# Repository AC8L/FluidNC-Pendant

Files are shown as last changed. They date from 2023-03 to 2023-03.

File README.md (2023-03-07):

# FluidNC-Pendant
Work originated from https://github.com/gjkrediet/Fluid-controller

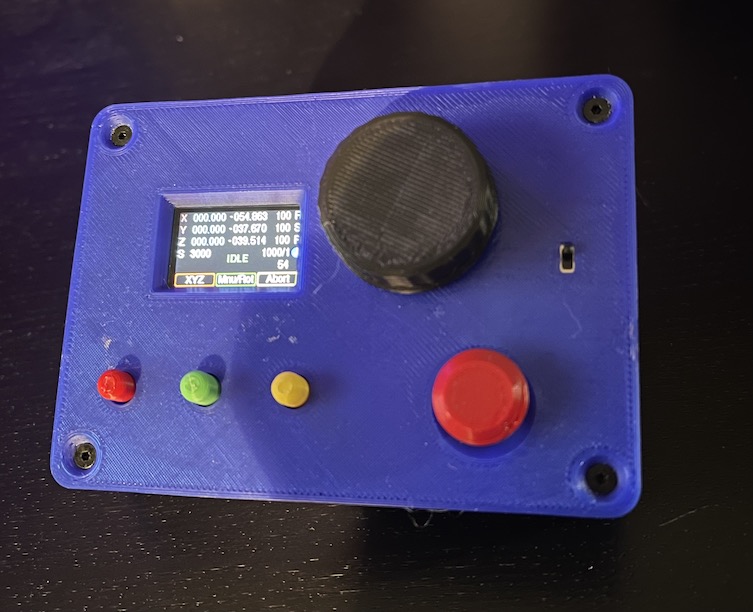
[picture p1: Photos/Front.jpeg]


The original design by gjkrediet was intended for bluetooth, this design is for Wi-Fi version of the FluidNC. Pendant communicates with the controller through Websocket protocol on TCP port 81.

# PCB
PCB was redesigned to hold all components to be soldered into it except the battery and power switch.
GRBL files are included for online order as well as schematics.

## Front of the PCB with soldered components
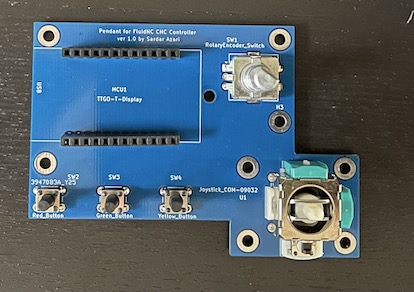
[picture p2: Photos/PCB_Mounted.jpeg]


## Back of the PCB
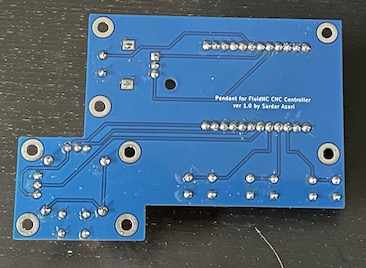
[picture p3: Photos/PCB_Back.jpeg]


## JST 2.0 soldered to the power switch and JST that comes with TTGO
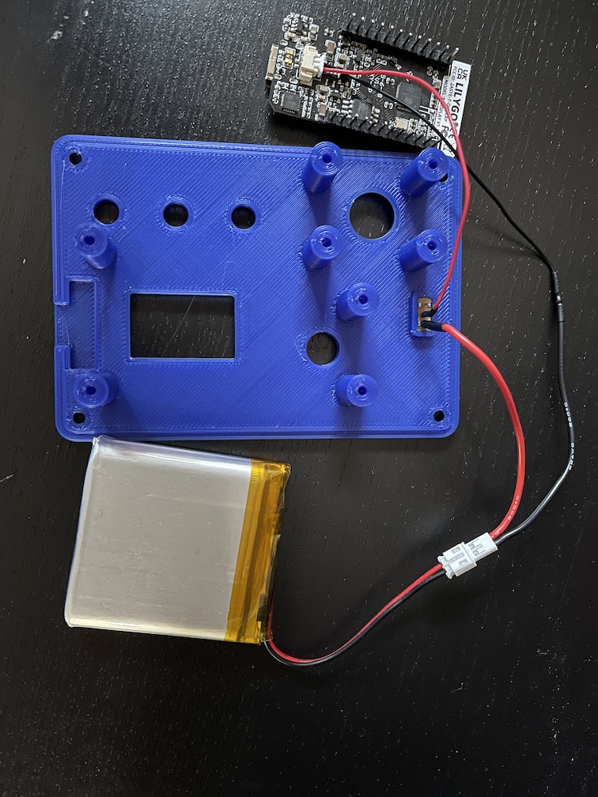
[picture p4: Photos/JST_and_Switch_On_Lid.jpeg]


## Battery is fixed behind PCB with a Kapton tape
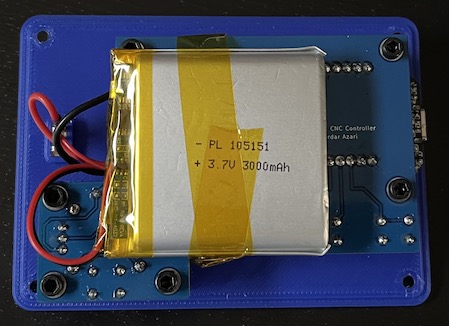
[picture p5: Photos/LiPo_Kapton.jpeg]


# 3D printed case
Lid was slightly modified to hold new PCB and power switch. Depending on which tactile switches were used - 3D printed buttons can be vertically scaled/reduced in the slicer.

# Firmware
Development was migrated from Arduino IDE into the PlatformIO to have stricter control over library versioning.
## Installation instructions:
1. Clone git repo: git clone https://github.com/AC8L/FluidNC-Pendant.git
2. Copy/rename sample_Config.h to Config.h
3. Enter your WiFi SSID information and FluidNC hostname/port in Config.h
4. Wait until Visual Studio Code pulls down all depending libraries
5. Overwrite content of .pio/libdeps/esp32dev/TFT_eSPI/User_Setup.h with the content of User_Setup.h.TFT_eSPI
6. Overwrite the content of .pio/libdeps/esp32dev/TFT_eSPI/User_Setup_Select.h with the content of User_Setup_select.h.TFT_eSPI
7. Now firmware will compile and you should be able to program the TTGO T Display.

# Operations
This section should probably be the largest section of this document but let at least get started.

## Red button
- When FluidNC is in ALARM mode, pressing RED button sends UNLOCK command
- Long pressing the RED button puts pendant into the sleep mode
- When in sleep mode, pressing RED button wakes pendant up

## Optical rotator
- By default it is in the mode of adjusting the jog speed
- When pressed - it enters the Menu mode. Menu options can be selected on the screen by scrolling the rotator and finally choosing by a click
- Homing can be done from Menu and changing brightness, turning spindle on and off among other functions

## Joystick
Jogs X and Y axes

## Green button
- Pressing GREEN button allows to change the default parameter that rotator controls.
- For example, after pressing the green button by rotating the rotator we can select the Z access to be controlled by rotator. Then we make a selection by pressing the GREEN button again and use rotator to bring the Z axis up and down.
## Yellow Button
Sends abort commands to the CNC

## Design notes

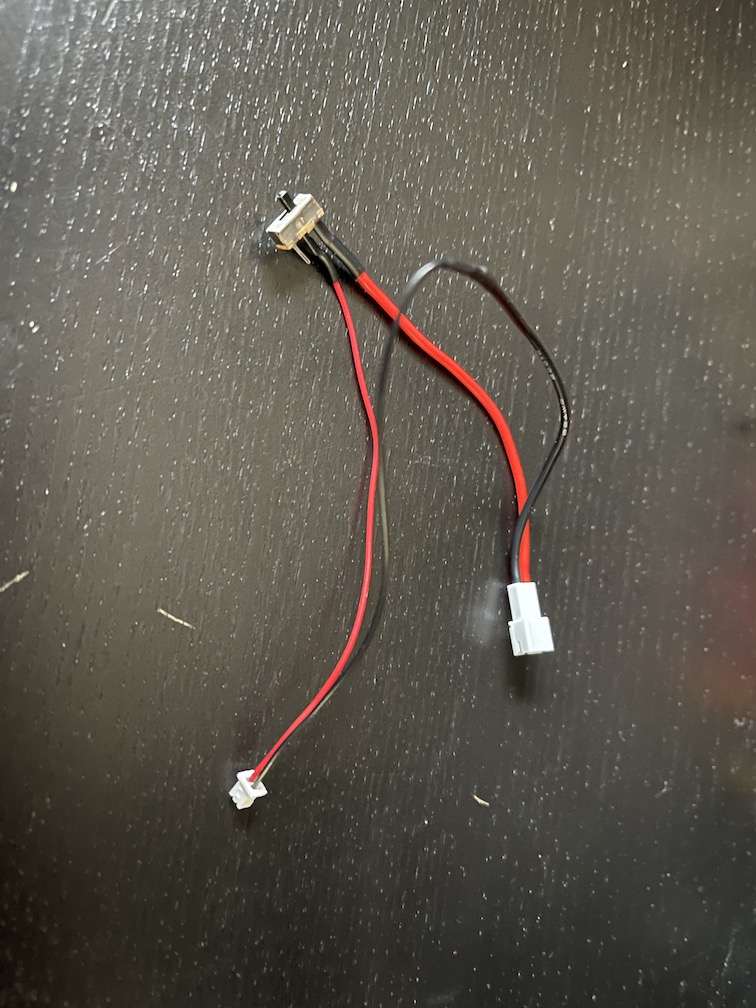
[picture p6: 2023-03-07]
Photos/JST_and_Switch.jpeg

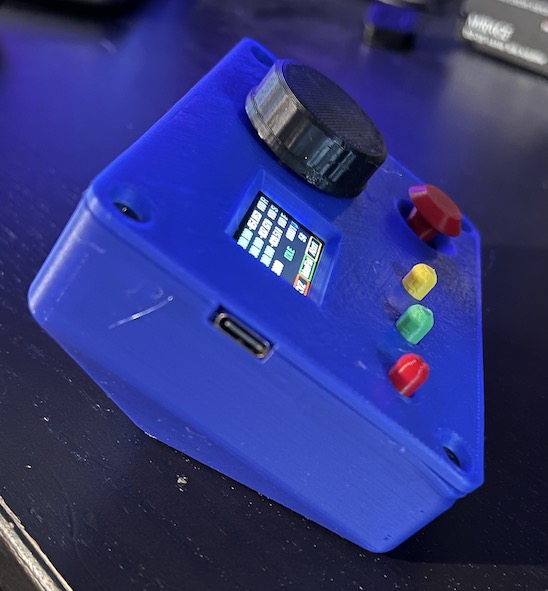
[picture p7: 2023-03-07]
Photos/Left.jpeg

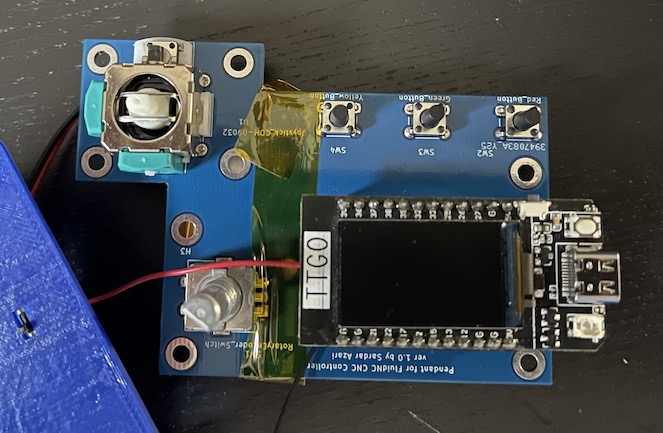
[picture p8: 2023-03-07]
Photos/Before fixing to lid.jpeg

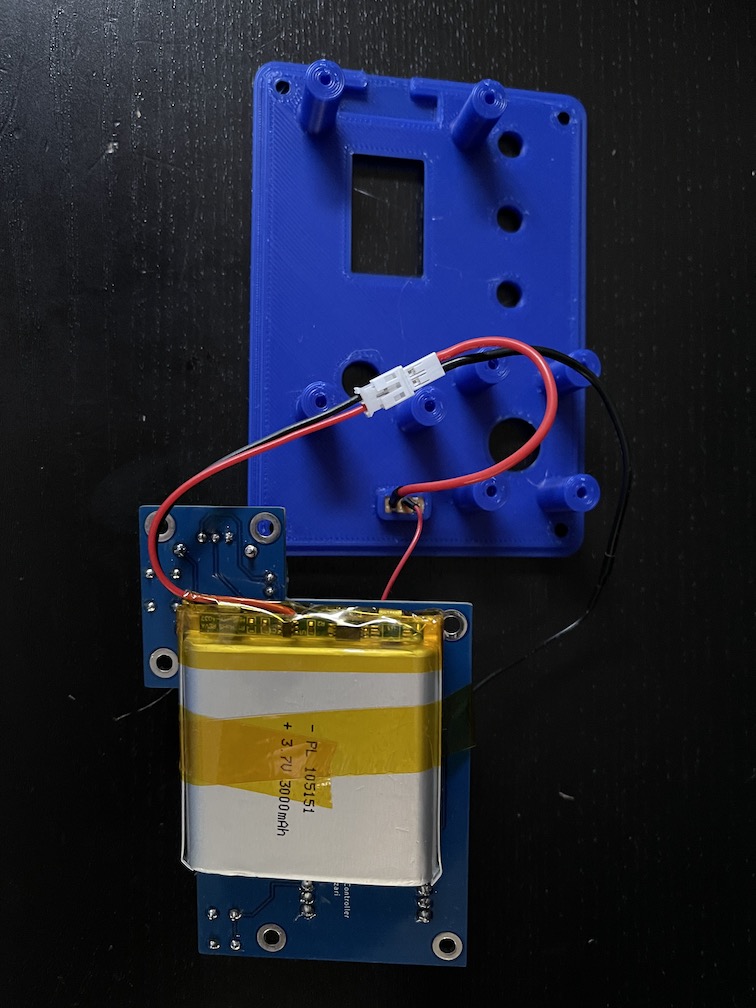
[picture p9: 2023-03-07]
Photos/BatteryAttached.jpeg

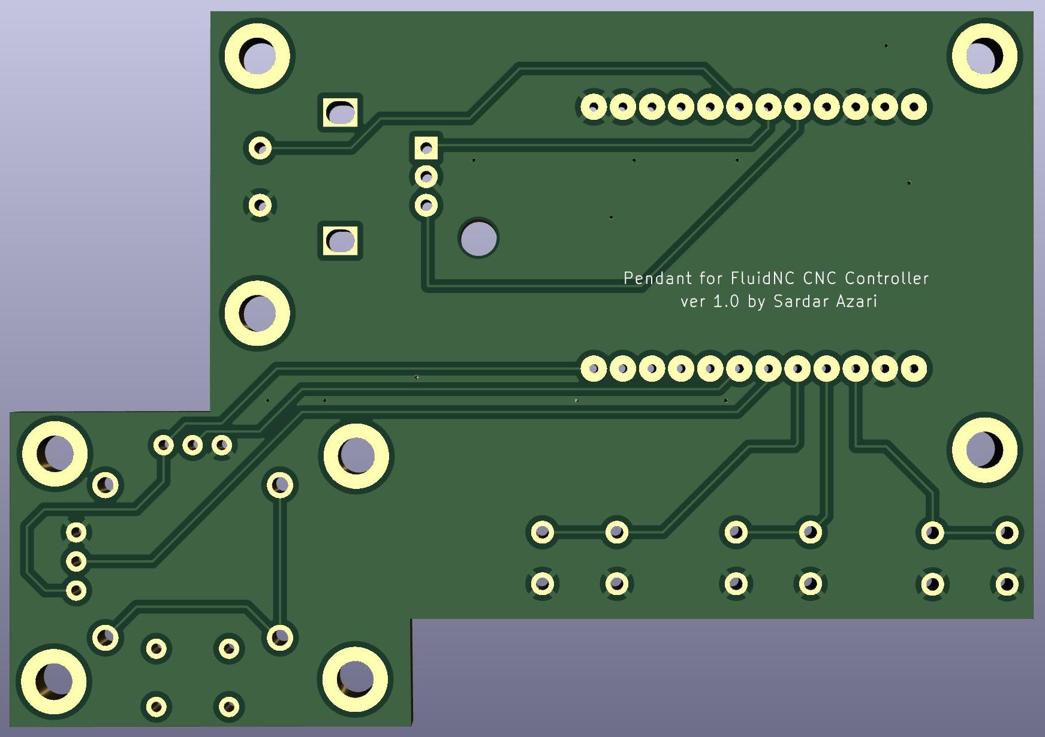
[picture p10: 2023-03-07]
PCB/FluidNC_Pendant_v2_Bottom.jpg

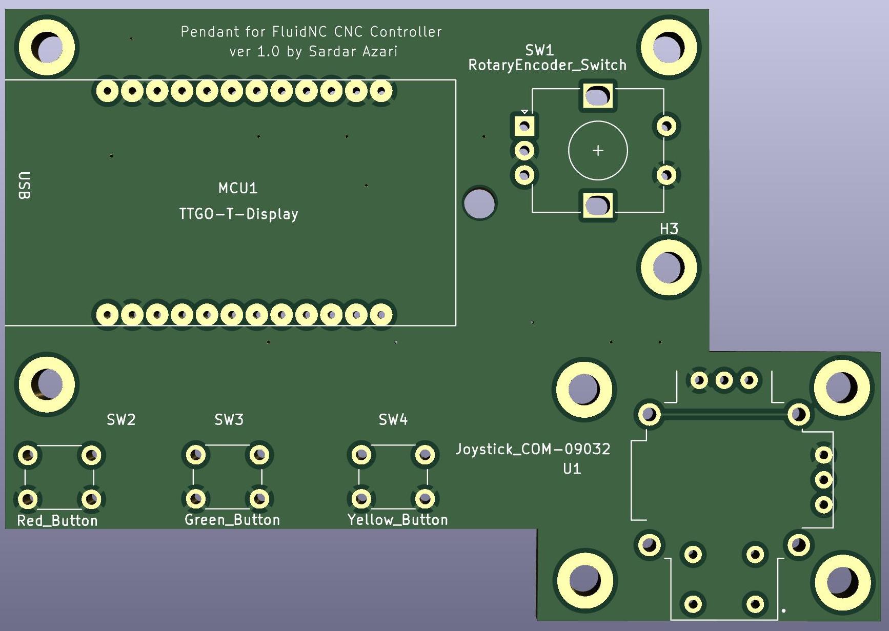
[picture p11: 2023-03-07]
PCB/FluidNC_Pendant_v2_Top.jpg

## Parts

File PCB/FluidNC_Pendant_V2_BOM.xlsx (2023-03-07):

Designator | Qnty | Description | Vendor/Link
MCU1 | 1 | LILYGO ESP32 T-Display Module | https://a.co/d/arEl3ou
SW1 | 1 | EC11 Rotary Encoder with switch | https://a.co/d/4C1LfQT
U1 | 1 | Joystick, 2 - Axis Analog (Resistive) Output | https://www.digikey.com/en/products/detail/sparkfun-electronics/COM-09032/6823623
SW2,SW3,SW4 | 3 | Tactile Switch SPST-NO Top Actuated Through Hole | https://www.digikey.com/en/products/detail/e-switch/TL1105DF160Q/271562
Battery | 1 | 3000mAh 105151 Lipo Battery with PH2.0mm JST Connector | https://a.co/d/7y6UerZ
JST | 1 | JST-PH 2.0 Female Connector Cable | https://a.co/d/fxLiYQF
SW5 | 1 | Switch, single pole double throw | https://www.digikey.com/en/products/detail/nkk-switches/MS12ANG03/1052824
 | 2 | 12 pin female head strip | https://a.co/d/bCoLMiA

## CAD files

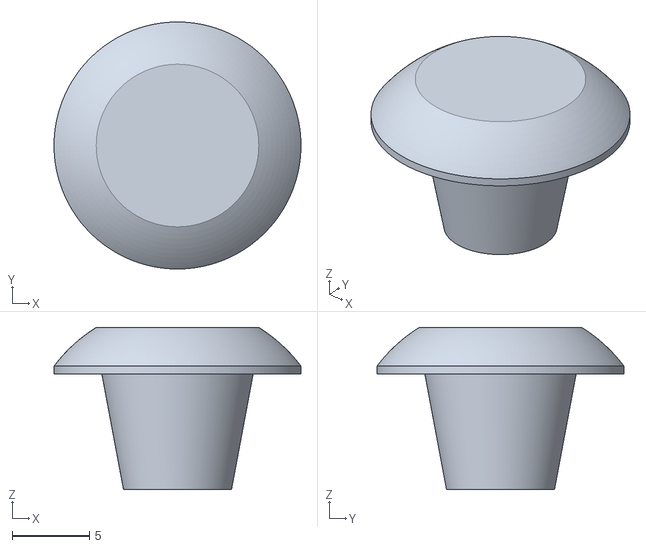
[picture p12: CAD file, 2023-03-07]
3D_Case/JoyStickKnob.stl
16.0 x 16.0 x 10.5

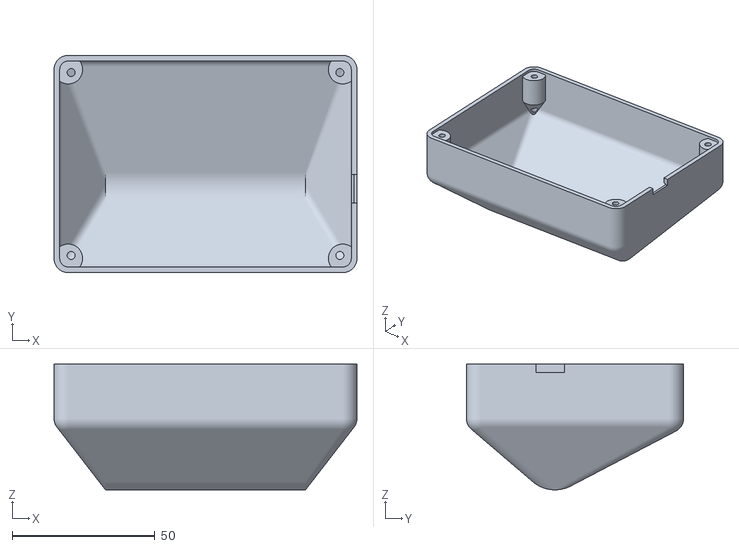
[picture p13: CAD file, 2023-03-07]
3D_Case/pendantV2_case.stl
106.0 x 76.0 x 44.0

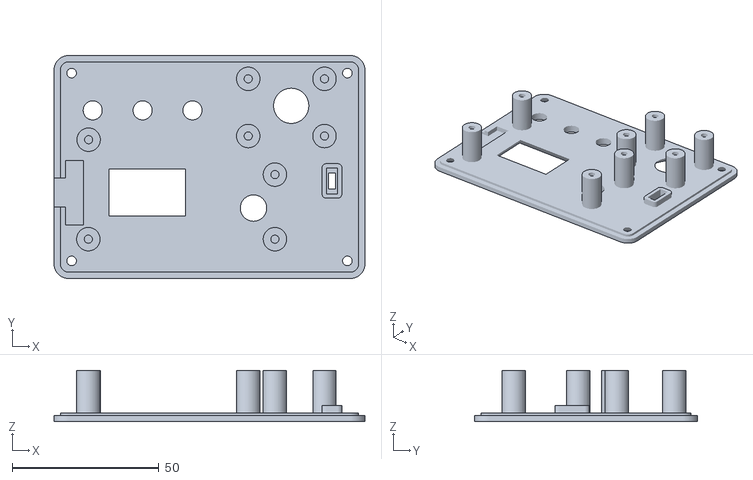
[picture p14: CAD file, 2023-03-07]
3D_Case/pendantV3_lid.stl
106.0 x 76.0 x 17.5

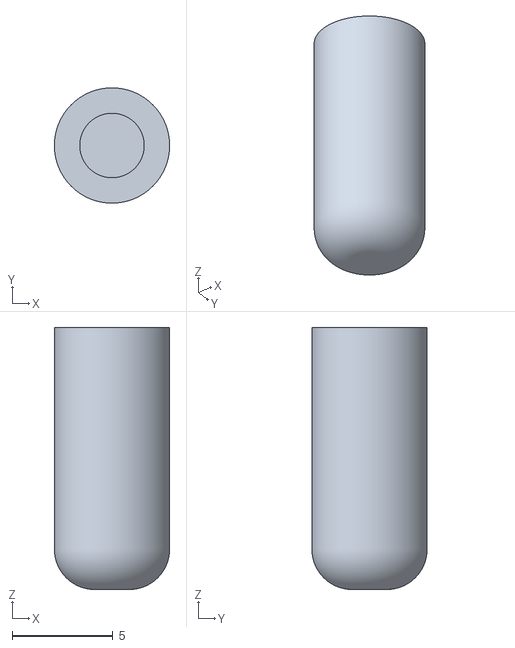
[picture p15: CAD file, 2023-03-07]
3D_Case/TactileSwitchButtonHead.stl
5.72 x 5.72 x 13.0

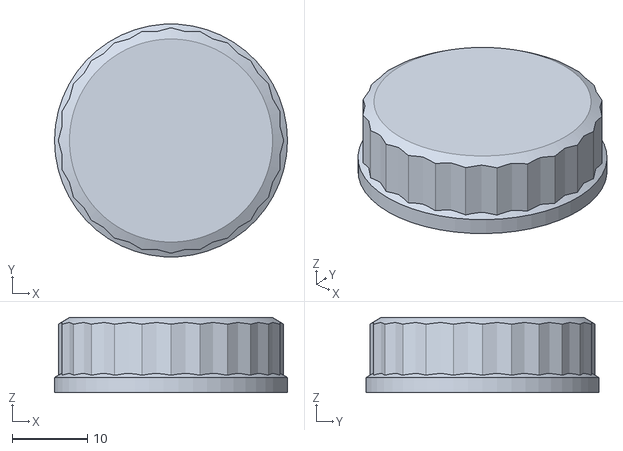
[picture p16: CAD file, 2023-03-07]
3D_Case/6mmShaftKnob.stl
31.0 x 30.9 x 10.0

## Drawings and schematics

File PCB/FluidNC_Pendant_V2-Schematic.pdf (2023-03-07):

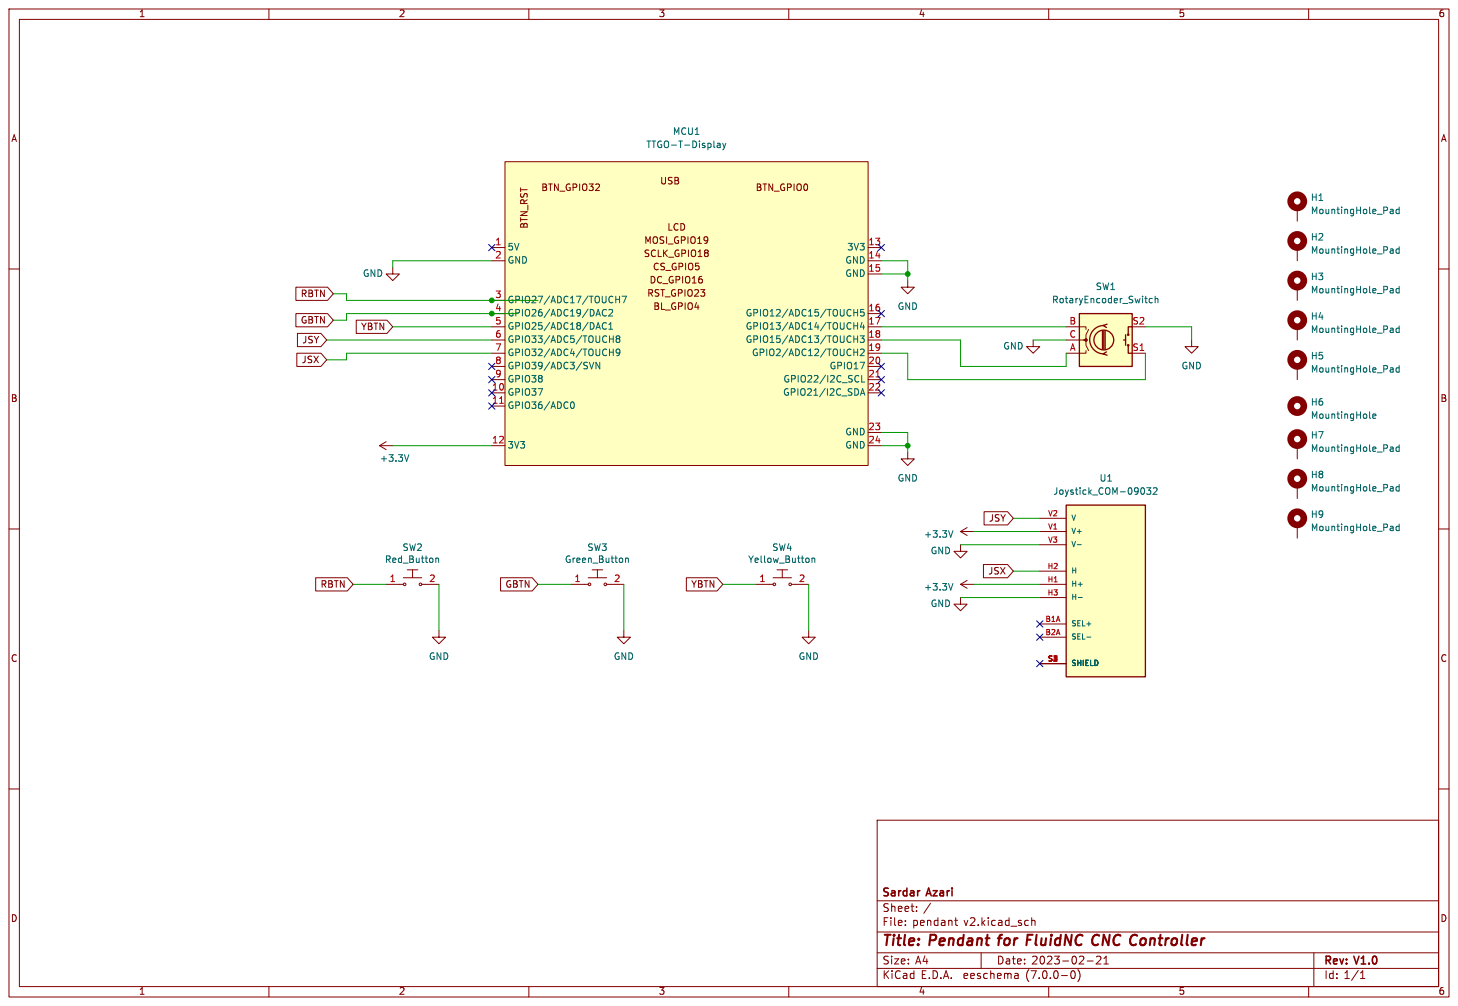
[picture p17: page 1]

Id: 1/1 Title: Pendant for FluidNC CNC Controller File: pendant v2.kicad_sch Sheet: / Sardar Azari

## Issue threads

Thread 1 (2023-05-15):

Unable to build

Prelo96, 2023-05-15:
Hi, i tried to build and load your program but i have some problem.
git cloned the repository
waited for all the depandanciens
config.h changed
file in .pio changed but no fortune at all:
log of the build

 *  Esecuzione dell'attività: C:\Users\prelo\.platformio\penv\Scripts\platformio.exe run

Processing esp32dev (platform: espressif32; board: esp32dev; framework: arduino)
-------------------------------------------------------------------------------------------------------------------------------------------------------------
Verbose mode can be enabled via `-v, --verbose` option
CONFIGURATION: https://docs.platformio.org/page/boards/espressif32/esp32dev.html
PLATFORM: Espressif 32 (2.1.0) > Espressif ESP32 Dev Module
HARDWARE: ESP32 240MHz, 320KB RAM, 4MB Flash
DEBUG: Current (esp-prog) External (esp-prog, iot-bus-jtag, jlink, minimodule, olimex-arm-usb-ocd, olimex-arm-usb-ocd-h, olimex-arm-usb-tiny-h, olimex-jtag-tiny, tumpa)
PACKAGES:
 - framework-arduinoespressif32 @ 3.10004.210126 (1.0.4)
 - tool-esptoolpy @ 1.30000.201119 (3.0.0)
 - toolchain-xtensa32 @ 2.50200.80 (5.2.0)
LDF: Library Dependency Finder -> https://bit.ly/configure-pio-ldf
LDF Modes: Finder ~ chain, Compatibility ~ soft
Found 33 compatible libraries
Scanning dependencies...
Dependency Graph
|-- TFT_eSPI @ 2.5.30
|-- RotaryEncoder @ 1.5.3
|-- SafeString @ 4.1.27
|-- AceButton @ 1.9.2
|-- FluidNC_WebSocket @ 1.0.0
|-- ArduinoOTA @ 1.0
|-- EEPROM @ 1.0.3
|-- WiFi @ 1.0
|-- Wire @ 1.0.1
Building in release mode
Compiling .pio\build\esp32dev\src\main.cpp.o
In file included from C:\Users\prelo\.platformio\packages\framework-arduinoespressif32\tools\sdk\include\newlib/stdio.h:47:0,
                 from C:\Users\prelo\.platformio\packages\framework-arduinoespressif32\cores\esp32/Arduino.h:27,
                 from src\Pendant.h:3,
                 from src\main.cpp:6:
C:\Users\prelo\.platformio\packages\framework-arduinoespressif32\tools\sdk\include\newlib/sys/reent.h:463:10: error: #if with no expression
Archiving .pio\build\esp32dev\lib194\libTFT_eSPI.a
In file included from .pio\libdeps\esp32dev\FluidNC_WebSocket\src/FluidNC_WebSocket.h:7:0,
                 from src\Pendant.h:9,
                 from src\main.cpp:6:
.pio\libdeps\esp32dev\SafeString\src/SafeString.h:138:0: warning: "F" redefined
 #define F(string_literal) (reinterpret_cast<const __FlashStringHelper *>(PSTR(string_literal)))
 ^
In file included from C:\Users\prelo\.platformio\packages\framework-arduinoespressif32\cores\esp32/Arduino.h:146:0,
                 from src\Pendant.h:3,
                 from src\main.cpp:6:
C:\Users\prelo\.platformio\packages\framework-arduinoespressif32\cores\esp32/WString.h:40:0: note: this is the location of the previous definition
 #define F(string_literal) (FPSTR(PSTR(string_literal)))
 ^
In file included from .pio\libdeps\esp32dev\TFT_eSPI/User_Setup_Select.h:61:0,
                 from .pio\libdeps\esp32dev\TFT_eSPI/TFT_eSPI.h:68,
                 from src\Pendant.h:18,
                 from src\main.cpp:6:
.pio\libdeps\esp32dev\TFT_eSPI/User_Setups/Setup25_TTGO_T_Display.h:18:0: warning: "TFT_CS" redefined
 #define TFT_CS              5
 ^
In file included from .pio\libdeps\esp32dev\TFT_eSPI/User_Setup_Select.h:30:0,
                 from .pio\libdeps\esp32dev\TFT_eSPI/TFT_eSPI.h:68,
                 from src\Pendant.h:18,
                 from src\main.cpp:6:
.pio\libdeps\esp32dev\TFT_eSPI/User_Setup.h:169:0: note: this is the location of the previous definition
 #define TFT_CS   PIN_D8  // Chip select control pin D8
 ^
In file included from .pio\libdeps\esp32dev\TFT_eSPI/User_Setup_Select.h:61:0,
                 from .pio\libdeps\esp32dev\TFT_eSPI/TFT_eSPI.h:68,
                 from src\Pendant.h:18,
                 from src\main.cpp:6:
.pio\libdeps\esp32dev\TFT_eSPI/User_Setups/Setup25_TTGO_T_Display.h:19:0: warning: "TFT_DC" redefined
 #define TFT_DC              16
 ^
In file included from .pio\libdeps\esp32dev\TFT_eSPI/User_Setup_Select.h:30:0,
                 from .pio\libdeps\esp32dev\TFT_eSPI/TFT_eSPI.h:68,
                 from src\Pendant.h:18,
                 from src\main.cpp:6:
.pio\libdeps\esp32dev\TFT_eSPI/User_Setup.h:170:0: note: this is the location of the previous definition
 #define TFT_DC   PIN_D3  // Data Command control pin
 ^
In file included from .pio\libdeps\esp32dev\TFT_eSPI/User_Setup_Select.h:61:0,
                 from .pio\libdeps\esp32dev\TFT_eSPI/TFT_eSPI.h:68,
                 from src\Pendant.h:18,
                 from src\main.cpp:6:
.pio\libdeps\esp32dev\TFT_eSPI/User_Setups/Setup25_TTGO_T_Display.h:20:0: warning: "TFT_RST" redefined
 #define TFT_RST             23
 ^
In file included from .pio\libdeps\esp32dev\TFT_eSPI/User_Setup_Select.h:30:0,
                 from .pio\libdeps\esp32dev\TFT_eSPI/TFT_eSPI.h:68,
                 from src\Pendant.h:18,
                 from src\main.cpp:6:
.pio\libdeps\esp32dev\TFT_eSPI/User_Setup.h:171:0: note: this is the location of the previous definition
 #define TFT_RST  PIN_D4  // Reset pin (could connect to NodeMCU RST, see next line)
 ^
In file included from .pio\libdeps\esp32dev\TFT_eSPI/User_Setup_Select.h:61:0,
                 from .pio\libdeps\esp32dev\TFT_eSPI/TFT_eSPI.h:68,
                 from src\Pendant.h:18,
                 from src\main.cpp:6:
.pio\libdeps\esp32dev\TFT_eSPI/User_Setups/Setup25_TTGO_T_Display.h:37:0: warning: "SPI_FREQUENCY" redefined
   #define SPI_FREQUENCY  40000000
 ^
In file included from .pio\libdeps\esp32dev\TFT_eSPI/User_Setup_Select.h:30:0,
                 from .pio\libdeps\esp32dev\TFT_eSPI/TFT_eSPI.h:68,
                 from src\Pendant.h:18,
                 from src\main.cpp:6:
.pio\libdeps\esp32dev\TFT_eSPI/User_Setup.h:357:0: note: this is the location of the previous definition
 #define SPI_FREQUENCY  27000000
 ^
In file included from .pio\libdeps\esp32dev\TFT_eSPI/User_Setup_Select.h:61:0,
                 from .pio\libdeps\esp32dev\TFT_eSPI/TFT_eSPI.h:68,
                 from src\Pendant.h:18,
                 from src\main.cpp:6:
.pio\libdeps\esp32dev\TFT_eSPI/User_Setups/Setup25_TTGO_T_Display.h:40:0: warning: "SPI_READ_FREQUENCY" redefined
 #define SPI_READ_FREQUENCY  6000000 // 6 MHz is the maximum SPI read speed for the ST7789V
 ^
In file included from .pio\libdeps\esp32dev\TFT_eSPI/User_Setup_Select.h:30:0,
                 from .pio\libdeps\esp32dev\TFT_eSPI/TFT_eSPI.h:68,
                 from src\Pendant.h:18,
                 from src\main.cpp:6:
.pio\libdeps\esp32dev\TFT_eSPI/User_Setup.h:363:0: note: this is the location of the previous definition
 #define SPI_READ_FREQUENCY  20000000
 ^
Compiling .pio\build\esp32dev\lib0e6\SafeString\BufferedOutput.cpp.o
Compiling .pio\build\esp32dev\lib0e6\SafeString\millisDelay.cpp.o
In file included from src\Pendant.h:18:0,
                 from src\main.cpp:6:
.pio\libdeps\esp32dev\TFT_eSPI/TFT_eSPI.h:970:8: warning: #warning >>>>------>> TOUCH_CS pin not defined, TFT_eSPI touch functions will not be available! [-Wcpp]
       #warning >>>>------>> TOUCH_CS pin not defined, TFT_eSPI touch functions will not be available!
        ^
Compiling .pio\build\esp32dev\lib9e8\AceButton\ace_button\AceButton.cpp.o
Compiling .pio\build\esp32dev\lib9e8\AceButton\ace_button\ButtonConfig.cpp.o
Compiling .pio\build\esp32dev\lib9e8\AceButton\ace_button\EncodedButtonConfig.cpp.o
Compiling .pio\build\esp32dev\lib9e8\AceButton\ace_button\LadderButtonConfig.cpp.o
Compiling .pio\build\esp32dev\lib9e8\AceButton\ace_button\testing\EventTracker.cpp.o
In file included from .pio\libdeps\esp32dev\SafeString\src\BufferedOutput.h:38:0,
                 from .pio\libdeps\esp32dev\SafeString\src\BufferedOutput.cpp:2:
.pio\libdeps\esp32dev\SafeString\src\SafeString.h:138:0: warning: "F" redefined
 #define F(string_literal) (reinterpret_cast<const __FlashStringHelper *>(PSTR(string_literal)))
 ^
In file included from C:\Users\prelo\.platformio\packages\framework-arduinoespressif32\cores\esp32/Arduino.h:146:0,
                 from .pio\libdeps\esp32dev\SafeString\src\BufferedOutput.cpp:1:
C:\Users\prelo\.platformio\packages\framework-arduinoespressif32\cores\esp32/WString.h:40:0: note: this is the location of the previous definition
 #define F(string_literal) (FPSTR(PSTR(string_literal)))
 ^
.pio\libdeps\esp32dev\SafeString\src\BufferedOutput.cpp: In member function 'void BufferedOutput::connect(Stream&, uint32_t)':
.pio\libdeps\esp32dev\SafeString\src\BufferedOutput.cpp:165:28: error: 'class Stream' has no member named 'availableForWrite'
     int avail = streamPtr->availableForWrite();
                            ^
.pio\libdeps\esp32dev\SafeString\src\BufferedOutput.cpp: In member function 'int BufferedOutput::internalStreamAvailableForWrite()':
.pio\libdeps\esp32dev\SafeString\src\BufferedOutput.cpp:303:24: error: 'class Stream' has no member named 'availableForWrite'
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
Prelo96, 2023-05-15:
Made some progress...
in platform.io changed the sintax to obtain the exact version of the depandancies
i still have some problem..

Processing esp32dev (platform: espressif32; board: esp32dev; framework: arduino)
---------------------------------------------------------------------------------------------------------------------------------------------------
Verbose mode can be enabled via `-v, --verbose` option
CONFIGURATION: https://docs.platformio.org/page/boards/espressif32/esp32dev.html
PLATFORM: Espressif 32 (2.1.0) > Espressif ESP32 Dev Module
HARDWARE: ESP32 240MHz, 320KB RAM, 4MB Flash
DEBUG: Current (esp-prog) External (esp-prog, iot-bus-jtag, jlink, minimodule, olimex-arm-usb-ocd, olimex-arm-usb-ocd-h, olimex-arm-usb-tiny-h, olimex-jtag-tiny, tumpa)
PACKAGES:
 - framework-arduinoespressif32 @ 3.10004.210126 (1.0.4)
 - tool-esptoolpy @ 1.30000.201119 (3.0.0)
 - toolchain-xtensa32 @ 2.50200.80 (5.2.0)
LDF: Library Dependency Finder -> https://bit.ly/configure-pio-ldf
LDF Modes: Finder ~ chain, Compatibility ~ soft
Found 33 compatible libraries
Scanning dependencies...
Dependency Graph
|-- TFT_eSPI @ 2.5.21
|-- RotaryEncoder @ 1.5.3
|-- SafeString @ 4.1.25
|-- AceButton @ 1.9.2
|-- FluidNC_WebSocket @ 1.0.0
|-- ArduinoOTA @ 1.0
|-- EEPROM @ 1.0.3
|-- WiFi @ 1.0
|-- Wire @ 1.0.1
Building in release mode
Archiving .pio\build\esp32dev\lib194\libTFT_eSPI.a
Archiving .pio\build\esp32dev\libefd\libRotaryEncoder.a
Compiling .pio\build\esp32dev\lib0e6\SafeString\BufferedOutput.cpp.o
Compiling .pio\build\esp32dev\lib0e6\SafeString\SafeStringStream.cpp.o
Compiling .pio\build\esp32dev\lib0e6\SafeString\SerialComs.cpp.o
Compiling .pio\build\esp32dev\lib0e6\SafeString\loopTimer.cpp.o
Compiling .pio\build\esp32dev\lib0e6\SafeString\millisDelay.cpp.o
Compiling .pio\build\esp32dev\lib9e8\AceButton\ace_button\AceButton.cpp.o
Compiling .pio\build\esp32dev\lib9e8\AceButton\ace_button\ButtonConfig.cpp.o
Compiling .pio\build\esp32dev\lib9e8\AceButton\ace_button\EncodedButtonConfig.cpp.o
.pio\libdeps\esp32dev\SafeString\src\BufferedOutput.cpp: In member function 'void BufferedOutput::connect(Stream&, uint32_t)':
.pio\libdeps\esp32dev\SafeString\src\BufferedOutput.cpp:164:28: error: 'class Stream' has no member named 'availableForWrite'
     int avail = streamPtr->availableForWrite();
                            ^
.pio\libdeps\esp32dev\SafeString\src\BufferedOutput.cpp: In member function 'int BufferedOutput::internalStreamAvailableForWrite()':
.pio\libdeps\esp32dev\SafeString\src\BufferedOutput.cpp:304:24: error: 'class Stream' has no member named 'availableForWrite'
     avail = streamPtr->availableForWrite();
                        ^
*** [.pio\build\esp32dev\lib0e6\SafeString\BufferedOutput.cpp.o] Error 1
=========================================================== [FAILED] Took 4.89 seconds ===========================================================

 *  Il processo del terminale "C:\Users\prelo\.platformio\penv\Scripts\platformio.exe 'run'" è stato terminato. Codice di uscita: 1.
 *  Terminale verrà
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

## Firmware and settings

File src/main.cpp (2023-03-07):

#define DEBUG

//#define MODE_BT
#define MODE_WIFI

#include "Pendant.h"

// Main loop ==========================================
unsigned long lastUpdate = millis();

void loop()
{
  sinceStart = millis();
  activeTimer(false);
  
  checkRotateA();
  checkJoystick();

  buttonREMS.check();
  buttonGREEN.check();
  buttonYELLOW.check();
  buttonRED.check();

  if (myCNC.isConnected() && lastUpdate + statusUpdateInterval<millis()){
        DEBUG_SERIAL.println("[MAIN] Status update...");
        checkBattery();
        getGrblState(true);
        checkConnect();
        tftUpdate(false);
        lastUpdate = millis();
    }

  if (rdX == 0 && rdY == 0 && rdZ == 0)
  {
    //buttonREMS.loop();
    //buttonGREEN.loop();
    //buttonYELLOW.loop();
  }
    //  Serial.print("."); //Check of er puntjes overblijven in de loop
}
// END of main loop =================================================

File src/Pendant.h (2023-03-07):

// Main Pendant declarations for FluidNC Pendant
//
#include <Arduino.h>

// Config file contains Wi-Fi connection details and FluidNC hostname/port
#include "Config.h"

#include <Wifi.h>
#include <FluidNC_WebSocket.h>

#include <Wire.h>
#include <RotaryEncoder.h>
#include <AceButton.h>
#include <WiFi.h>
#include <ArduinoOTA.h>
#include <EEPROM.h>
#include <esp_wifi.h>
#include <TFT_eSPI.h>      // Hardware-specific library
using namespace ace_button;

#define EEPROM_SIZE 1

TFT_eSPI tft = TFT_eSPI(); // Invoke custom library

RotaryEncoder *encoderA = nullptr;

// I/O pin definitions
#define PIN_REM1 GPIO_NUM_15
#define PIN_REM2 GPIO_NUM_13
#define PIN_JSX GPIO_NUM_32
#define PIN_JSY GPIO_NUM_33
#define PIN_REMS GPIO_NUM_2
#define PIN_YELLOW GPIO_NUM_25
#define PIN_GREEN GPIO_NUM_26
#define PIN_RED GPIO_NUM_27
#define PIN_JS_VCC GPIO_NUM_17
#define PIN_BATT 34
#define ADC_EN  14

#define TFT_LEFT    1
#define TFT_CENTER  2
#define TFT_RIGHT   3
#define TFT_TRANSP  true
#define TFT_OBLQ  false
#define TFT_LIGHTBLUE 0x86FF
#define TFT_LIGHTRED 0xF9E7
#define TFT_DARKBLUE 0x0018
#define TFT_OVERYELLOW 0xFF35
#define TFT_MEDIUMGREEN 0x04A2
#define TFT_DARKRED 0xA800
#define TFT_MEDIUMBLUE 0x3D5F
#define TFT_DARKORANGE 0xFAC0

#define MAX_JOGSTR 50
#define MAX_STATUSSTR 50
#define POWEROFF_TIME 300
#define LINEHEIGHT_DEF  22

enum pendantstate {
  Menu,
  MenuConfirm,
  Pendant,
  RotateChoice,
  MenuSpindleSpeed,
  MenuBrightness
};

enum menuOptions {
  poweroff,
  spindlespeed,
  spindleonoff,
  steps,
  quit,
  home,
  setwxy0,
  setwz0,
  probe,
  gawxy0,
  unlock,
  resetgrbl,
  brightness
};

enum rotorDestin  {
  RotXaxis,
  RotYaxis,
  RotZaxis,
  RotSpindlespeed,
  RotJogspeed,
  RotOvfeed,
  RotOvspeed,
  RotOvrapid
};

enum joystickDestin {
  jsXYaxis,
  jsZaxis
};

volatile pendantstate pState = Pendant;
volatile menuOptions menuState = quit;
volatile rotorDestin rState = RotJogspeed;
volatile joystickDestin jState = jsXYaxis;

const int maxMenu = 12;
const int jogSpeedMax = 5000; //dit moet gelijk lopen met de settings in config.yaml
static char mStateStr[][11] { "? ?", "ALARM", "IDLE", "JOG", "HOME", "CHECK", "RUN", "CYCLE", "HOLD", "SAFE", "SLEEP" };
const int powerOffTime = 60;
volatile bool powerOffNow = false;

String name = "FluidNC";

FluidNC_WS myCNC = FluidNC_WS();

#define DEBUG_SERIAL Serial

char statusStr[MAX_STATUSSTR];
volatile char g_sbuf[128];
volatile byte menuChoice = 0, backLight = 1;
volatile unsigned long lastJogCmdXYZ = 0, lastStepCmdXYZ = 0;
unsigned long tExec = 1000;
unsigned long statusUpdateInterval = 1000;
const int updateInterval = 198;
volatile float distX = 0, distY = 0, distZ = 0;
volatile int battVolt;
unsigned long sinceStart, lastGrblState;
int rdX = 0, rdY = 0, rdZ = 0, multXYZ = 0;
int calibrateX, calibrateY;
//float mX, mY, mZ;  //Machine positions
//float wX, wY, wZ;  //Work positions
RTC_DATA_ATTR int jogSpeed = 1000; //Overleeft een herstart vanuit sleep
int jogSpeedDisp = 0, setSpindleSpeed = 3000, spindleDisp = -1;
//int reportedSpindleSpeed = 0;
//int ovSpeed = 0, ovFeed = 0, ovRapid = 0;
//bool spindleOn = false;
volatile bool smallSteps = false;
volatile int stepXYZ = 0;
AceButton buttonREMS, buttonGREEN, buttonYELLOW, buttonRED;

// Predeclare functions
void ConnectWiFi(void);
void otaLoop(void);
IRAM_ATTR void checkPositionA(void);
void forceEndJog(void);
void waitEndJog(void);
int readJSX(void);
int readJSY(void);
int checkJoystick(void);
void checkRotateA(void);
void checkBattery(void);
void printAxisCoords(float m, float w, byte row);
void printCircleBlue (byte x, byte y);
void tftPrintAllButtons();
void tftPrintButtonOrange(String txt);
void tftPrintButtonGreen(String txt);
void tftPrintButtonRed(String txt);
void tftPrintButton(int bc, int tc, byte col, byte row, byte len, String txt);
void tftUpdate(bool force);
void tftPrint(int align, bool transp, int fg, int bg, byte col, byte row, byte len, String txt);
void tftPrintBig(int bg, int fg, byte col, byte row, byte len, String txt);
void tftPrintColor(int color, byte col, byte row, String txt);
void tftPrintSimple(byte col, byte row, String txt);
void activeTimer(bool reset);
void getGrblState(bool full);

#include "SleepTimer.h"
#include "Menu.h"
#include "ButtonHandlers.h"
#include "Joystick.h"
#include "Rotator.h"
#include "TFT_Draw.h"
#include "Setup.h"
#include "Misc.h"
